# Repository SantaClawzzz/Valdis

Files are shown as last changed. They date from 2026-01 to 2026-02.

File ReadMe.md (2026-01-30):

# Valdis

## First test bench<br>
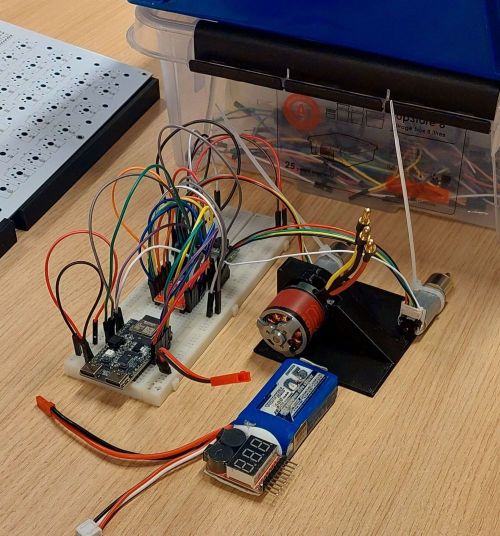
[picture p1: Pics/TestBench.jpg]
Test


## Info

**HETKEL PINOUT ON KÕIK VALE**<br>
Läksime üle PCB designile ja kasutuses nüüd ESP32 S3 (NanoS3)

**Mini-battle bot Läti võistluseks (450g)**

### Komponendid

* 3-phase relva mootor
* ESC ([Emax_bullet_35A](https://www.hobbydrone.cz/en/emax-bullet-35a/))
* 2x Mootorit liikumiseks (kursuse omad)
* 1x TB6612FNG ([Kiip](https://www.digikey.com/en/products/detail/toshiba-semiconductor-and-storage/tb6612fng-c-8-el/1730070) mitte breakout)
* 1x ESP32-S3 ([NanoS3](https://unexpectedmaker.com/shop.html#!/NanoS3/p/577095557/category=0))
* 3S aku
* USB-C ([USB4085-GF-A](https://www.digikey.com/en/products/detail/gct/USB4085-GF-A/9859662))
* Switching 3.3V ([RAA2118054GP3#JA0](https://www.digikey.com/en/products/detail/renesas-electronics-corporation/RAA2118054GP3-JA0/22162357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))

Kasutusse võtti ESP32-S3 (NanoS3 devkit)<br>
Meil vaja 13:<br>
* Driver võtab 3per mootor = 6 kokku
* Mootori enkooderid veel 2x2=4 kokku
* ESC võtab PWM, ehk 1 kokku
* EN nupp = 1 kokku
* Buzzer = 1 kokku

Lisaks on vaba pinne 7tk (+3 power pin):
* IO35
* IO36
* IO37
* IO9 (SCL)
* IO8 (SDA)
* RX
* TX

Power:
* 5V
* 3V3
* GND

### Keha

Keha tuleks Resin või mingi 3D print, kõik komponendid kaaluvad 202g, ehk 230g enam vähem mängimis ruumi.<br>
Enne tehtud proto (mis ka liiga väike), on 64g, et suht OK

Relvale teha mingi lindiga või sarnane ülekande mehhanism, et saaks mootori keresse peita ja ei saaks otse laksu teistelt

### Proge/RC

Kaugelt juhib läbi bluetoothi, arvatavasti sama millega Jaan juhib<br>
Puldiks võtta mingi Xbox controller millel on bluetooth receiver juba olemas

### MCU pinout

* Mootorid:
  * PWM
    * PWMA - IO15
    * PWMB - IO10
  * A IN
    * AIN2 - IO14
    * AIN1 - IO13
  * B IN
    * BIN2 - IO11
    * BIN1 - IO12

  * Enkooder Mootor 1 (A)
    * Kollane (B) - IO16
    * Roheline (A) - IO17
  * Enkooder Mootor 2 (B)
    * Kollane (B) - IO6
    * Rohleine (A) - IO7

* ESC PWM - IO18

* Buzzer - IO34

* DBG LED - IO5

* BAT VOL - IO1

### Power

* 12V aku - regulator - 3.3V
  * 3.3V toidab MCU ja DRV loogika ja enkooderi VCC
* 12V toidab DRV switching
* STBY - otse 3.3V ehk HIGH ja constant ON

Toite jaoks on analoog pin mis mõõdab seda
* Selle jaoks pinge jagur (1000R/200R, 12.6V/10.8V)
  * 2.1V when full
  * 1.8V when empty (just kui)

### Enkooder

Enkoodril on 7x35 impulssi pöörde kohta (just kui)<br>
Vaja teha koodis et kontrolliks kiirust ja hoiaks sama erinevalt pingest ja nh soidaks ka otse kui uks vasib ara

### ESC

ESC on väline, joodab otse külge, kannatab 35A ja on current surge protection ka olemas

### Switch

Power switch ühendub JST-PH-2.0 pistikuga, ja power lüliti kontroll on low-side FET

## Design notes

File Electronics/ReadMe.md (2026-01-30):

# Info

Skemaatik ja elektroonika muudatused kõik siia<br>

## Rev_1

Esimene rev mis ei jõudnud kaugemale arendusest oli joodetud otse protoboardile ESP-C6, TB6612FNG driver, buzzer, Regu ja headerid<br>
See ei läinud kasutusse sest on vaja S3 kergemaks Bluetooth ühenduseks, sest Liikmel juba kood olemas, C6 ei võimalda BluePad library (kui sain õigesti aru)

Seega S3 peale minek oli kõige loogilisem, aga S3 on palju suurem, uue ostmine pold halb idee, aga esimese deadline liikus edasi, sest unustasime regada, et läks korralikuma PCB designi peale, ehk Rev_2

## Rev_2

Teine Rev oli PCB design aga kasutades DevKiti, sest ei taha tekitada rohkem probleeme mida ei saa pärast hotfixiga parnada. Kui see töötab, siis ideaalis on Rev_3 see kui PCBl vahetatakse DevKit reaalse MCU-ga ära
Praegusel disainil on NanoS3, mis ei ole USB ühendusega, aga on toodud need pinnid välja. Switching regu on pandud selle toiteks ja LDO oleks võibolla old kahtlane (100-200mA ja 12.6V pealt 3.3V peale).

Loomulikult ka USB-C ja ka mitu erinevat headeri, mõned tavaliste gpiode jaoks, aku, switchi (power switch on FET controlled (Low side, sest high current suht)) ja ka mootorid.

Disain ise on 4 layer, Signal-GND-GND-Signal (Aku ja Fet polyd on kõigil neljal layeril, et oleks rohkem vaske jahutuseks)

Nano ise joodetakse SMD kujul peale, ning keskmine EPAD seal all samuti.

DBG LEDi kõrvale on veel kõigi 3 toite LEDid, 12V, 5V, 3V3

# Docs

## Schematic

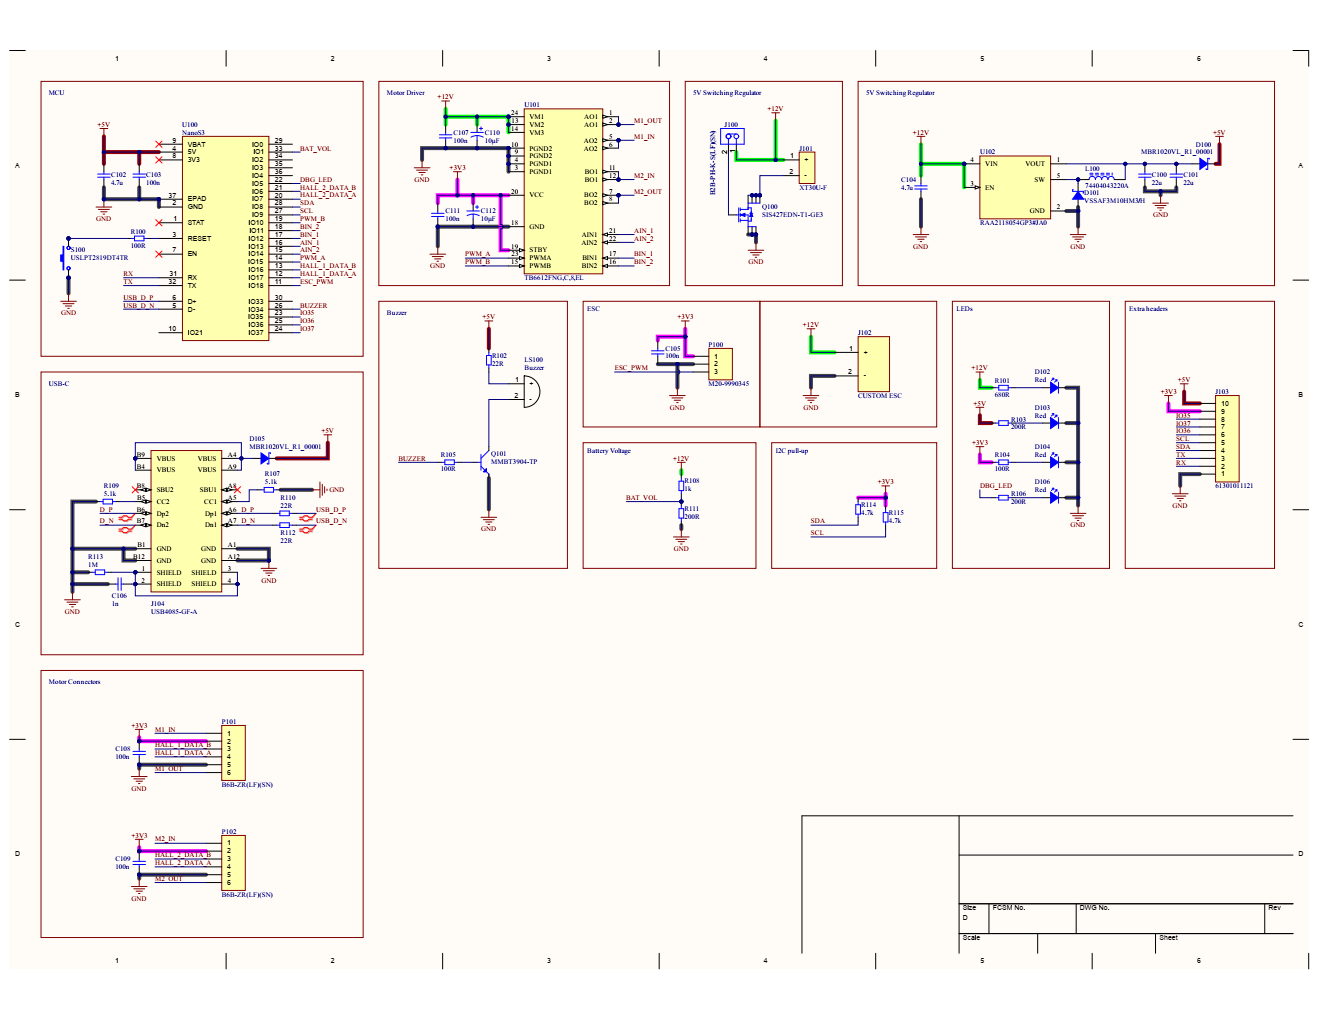
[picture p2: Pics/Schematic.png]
Schematic


## Layout

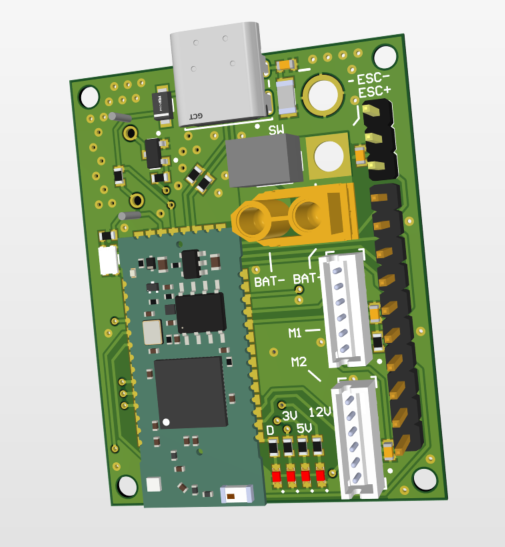
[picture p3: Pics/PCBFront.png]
PCBFront

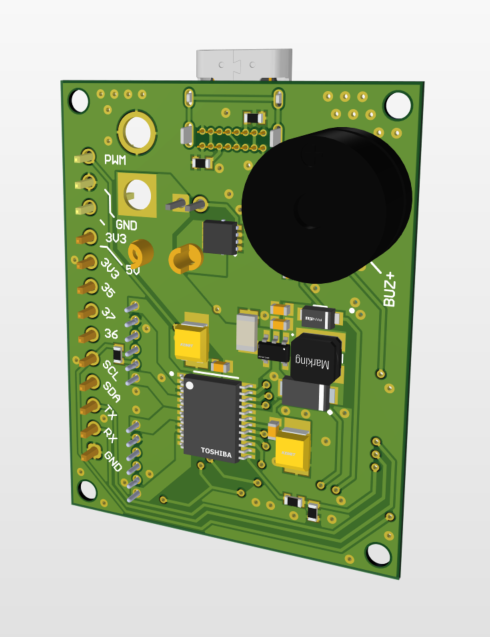
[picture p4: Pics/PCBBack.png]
PCBBack


## ESP32-S3 (NanoS3) pinout

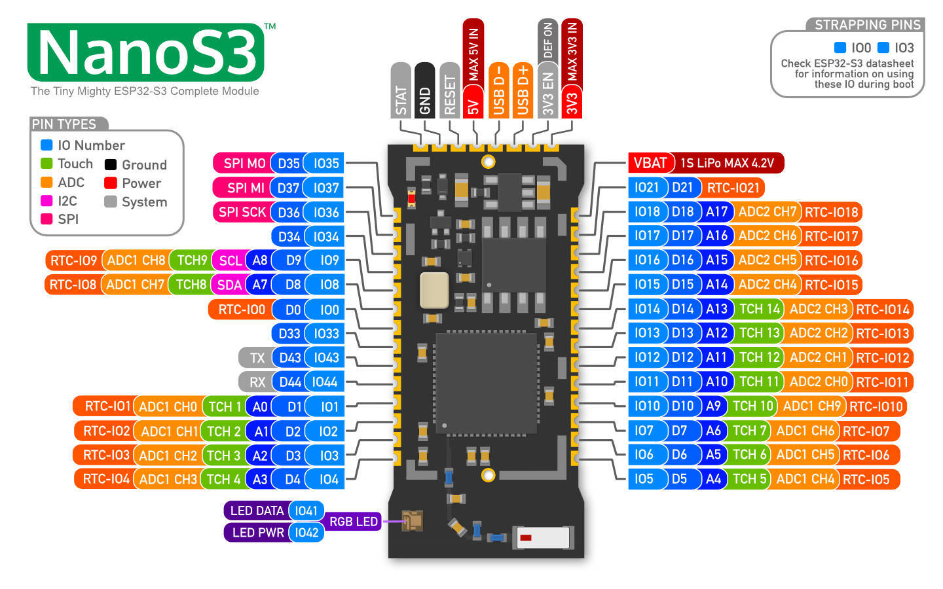
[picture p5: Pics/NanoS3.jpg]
ESPPinout


## Motor pinout

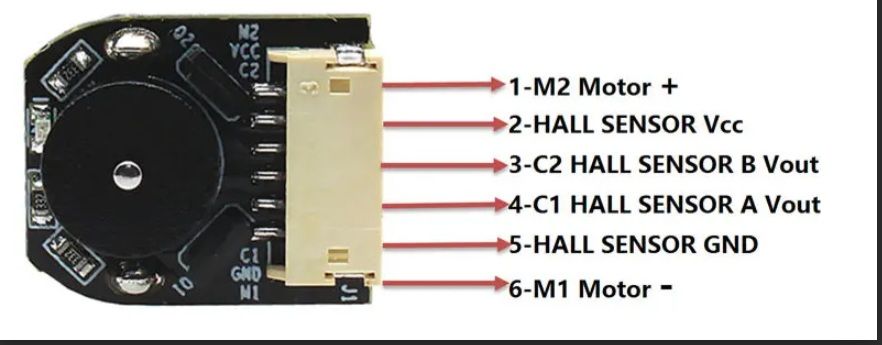
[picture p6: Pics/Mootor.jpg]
MotorPinout


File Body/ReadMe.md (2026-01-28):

# Info

Kui peaks mingi 3D mudelid või mingid pildid jms, siis tuleb siia
3D kehad PCBst on lisatud

# Docs

## Old Body 3D model

OldBody

## Body 3D model

Body

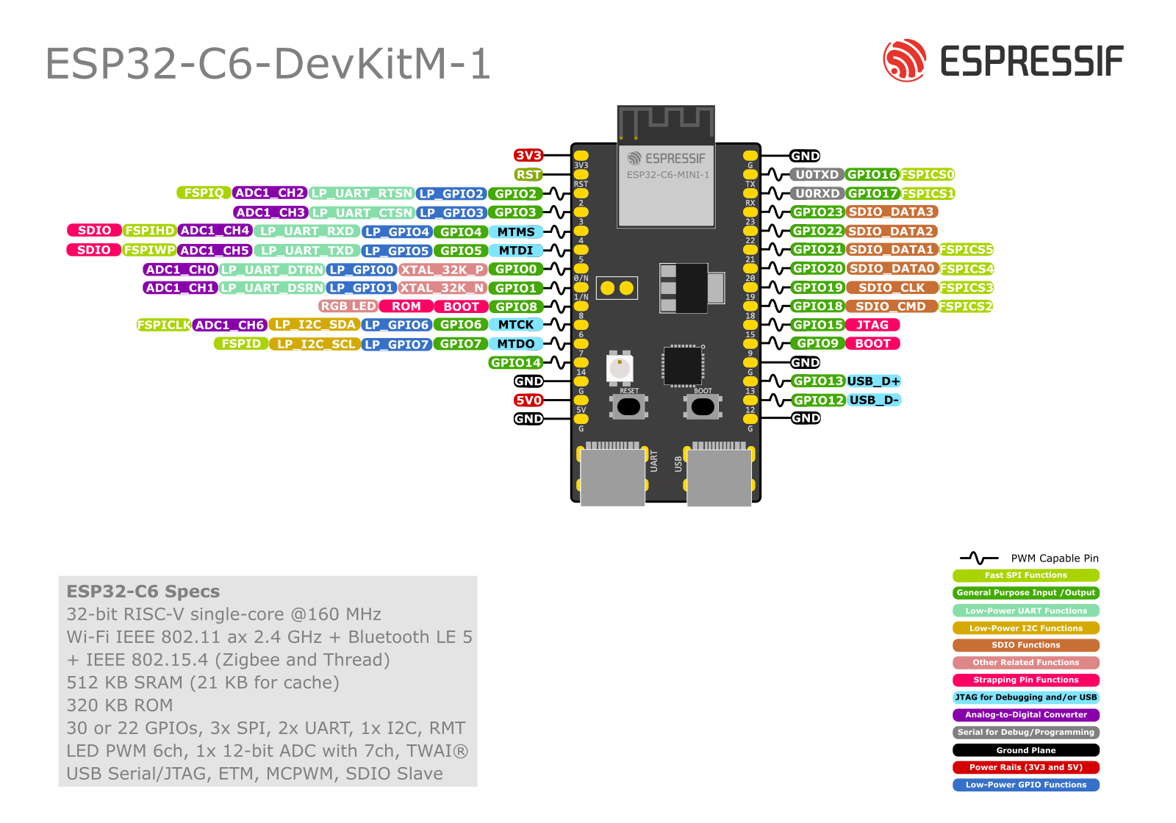
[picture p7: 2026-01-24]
Pics/ESP32-C6-DevKit-M1.png

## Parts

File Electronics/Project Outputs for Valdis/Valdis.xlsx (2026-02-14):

Comment | Description | Designator | Footprint | LibRef | Quantity
22u | MLCC, 0603, 22u, 10%, 16V, X5R | C100, C101 | MLCC_0603_M | CMP-001-1264-1 | 2
4.7u | MLCC, 0805, 4.7u, 10%, 50V, X5R | C102 | MLCC_0805_M | CMP-001-0828-2 | 1
100n | MLCC, 0603, 100n, 10%, 35V, X7R, MLCC, 0603, 100n, 10%, 50V, X7R | C103, C105, C107, C108, C109, C111 | MLCC_0603_M | CMP-001-0755-1, CMP-001-0815-1 | 6
4.7u | MLCC, 1206, 4.7u, 10%, 35V, X5R | C104 | MLCC_1206_M | CMP-001-1124-2 | 1
1n | MLCC, 0603, 1n, 10%, 50V, X7R | C106 | MLCC_0603_M | CMP-001-0786-1 | 1
T495B106K025ATE750 | 10UF Solid MNO2 Tantalum Electrolytic Capacitor, 25 V DC +/-10%, T495 Series | C110, C112 | 593D106X9025C2TE3-Footprint-1 | CMP-0001-00298-2 | 2
MBR1020VL_R1_00001 | Rectifier Diode, Schottky, 1 Phase, 1 Element, 1A, 20V V(RRM), Silicon | D100, D105 | FP-MBR1020VL_R1_00001-MFG | CMP-ROOT-01310-1 | 2
VSSAF3M10HM3/H | Rectifier Diode, Schottky, 1 Phase, 1 Element, 2.3A, 100V V(RRM), Silicon, DO-221AC | D101 | VSSAF3M10HM3_H-Footprint-1 | CMP-ROOT-01308-1 | 1
Red | Generic red 0603 LED | D102, D103, D104, D106 | 0603 RED LED | CMP-ROOT-00025-2 | 4
B2B-PH-K-S(LF)(SN) | Connector Header, PH Series, 2 Position, 2.00mm, Through Hole, Press-Fit, Solder, Natural | J100 | JST-B2B-PH-K-S_V | CMP-ROOT-01319-1 | 1
XT30U-F | Power Connector | J101 | XT30U-F | CMP-ROOT-01262-2 | 1
CUSTOM ESC | Custom ESC pinout | J102 | CUSTOM ESC-Footprint-1 | CMP-ROOT-01320-3 | 1
61301011121 | THT Vertical Pin Header WR-PHD, Pitch 2.54 mm, Single Row, 10 pins | J103 | 61301011121 | CMP-ROOT-01212-1 | 1
USB4085-GF-A | USB Connector, 16 Contact(s), Female, Right Angle, Solder Terminal, Locking, Receptacle | J104 | FP-USB4085-GF-A-MFG | CMP-001-1800-1 | 1
74404043220A | General Purpose Inductor, 22uH, 20%, 1 Element, Nickel-zinc Ferrite-Core, SMD, 1616 | L100 | WE-LQS_4025 | CMP-ROOT-01309-1 | 1
Buzzer | 7mm | LS100 | Buzzer-Footprint-1 | CMP-ROOT-01315-3 | 1
M20-9990345 | Connector Header Through Hole 3 position 0.100" (2.54mm) | P100 | 3Pos Pin Header | CMP-ROOT-00217-1 | 1
B6B-ZR(LF)(SN) | Header for PCB; pitch 1.50mm; 6-contacts; THT; male; top entry; 50V/1A | P101, P102 | FP-B6B-ZR-SM4-TF_LF_SN-MFG | CMP-ROOT-01270-3 | 2
SIS427EDN-T1-GE3 | Trans MOSFET P-CH 30V 15A 8-Pin PowerPAK EP T/R | Q100 | Copy of TPN2R304PL,L1Q-Footprint-1 | CMP-ROOT-01317-1 | 1
MMBT3904-TP | TRANS NPN 40V 0.2A SOT23 | Q101 | SOT-23-3 | CMP-ROOT-00274-1 | 1
100R | Resistor, 0603, 100R, 1%, 1/10W, Resistor, 0603, 100R, ≤5%, ≥1/16W | R100, R104, R105 | Resistor_0603_M | CMP-001-0054-5, CMP-0001-00262-1 | 3
680R | Resistor, 0603, 680R, 1%, 1/10W | R101 | Resistor_0603_M | CMP-001-0074-3 | 1
22R | Resistor, 0603, 22R, 1%, 1/10W | R102, R110, R112 | Resistor_0603_M | CMP-001-0038-3 | 3
200R | Resistor, 0603, 200R, 1%, 1/10W, Resistor, 0603, 220R, 1%, 1/10W | R103, R106, R111 | Resistor_0603_M | CMP-001-0060-2, CMP-001-0061-2 | 3
5.1k | Resistor, 0603, 5.1k, 1%, 1/10W | R107, R109 | Resistor_0603_M | CMP-001-0094-2 | 2
1k | Resistor, 0603, 1k, 0.1%, 1/16W | R108 | Resistor_0603_M | CMP-0001-00237-1 | 1
1M | Resistor, 1206, 1M, 1%, 1/4W | R113 | Resistor_1206_M | CMP-0001-00051-1 | 1
4.7k | Resistor, 0603, 4.7k, 1%, 1/10W | R114, R115 | Resistor_0603_M | CMP-001-0093-2 | 2
USLPT2819DT4TR | Keypad Switch, SPST, 0.05A, 1.96N, Solder Terminal, Panel Mount | S100 | USLPT2819DT4TR-Footprint-1 | CMP-ROOT-01290-3 | 1
NanoS3 | Unexpected Maker's NanoS3 DevKit | U100 | NanoS3 | CMP-00023-1 | 1
TB6612FNG,C,8,EL | DC Motor Driver 2.7V to 5.5V 24-Pin SSOP Embossed T/R | U101 | FP-SSOP24-P-300-0_65A-MFG | CMP-00025-1 | 1
RAA2118054GP3#JA0 | Switching Regulator, Current-mode, 0.3A, 230kHz Switching Freq-Max, PDSO5 | U102 | P5_064B_MFG | CMP-00019-3 | 1

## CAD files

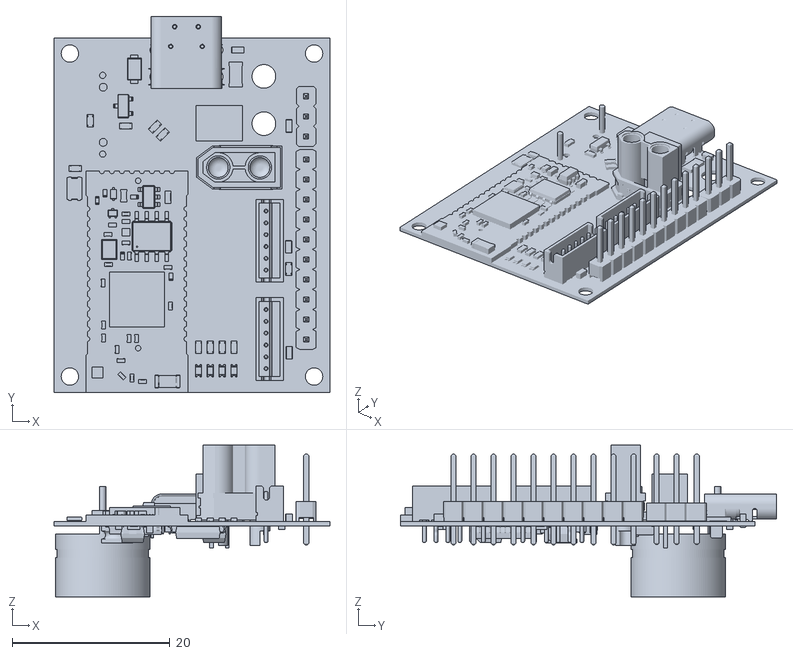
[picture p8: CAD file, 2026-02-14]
Body/Valdis.stl
35.0 x 47.7 x 19.3

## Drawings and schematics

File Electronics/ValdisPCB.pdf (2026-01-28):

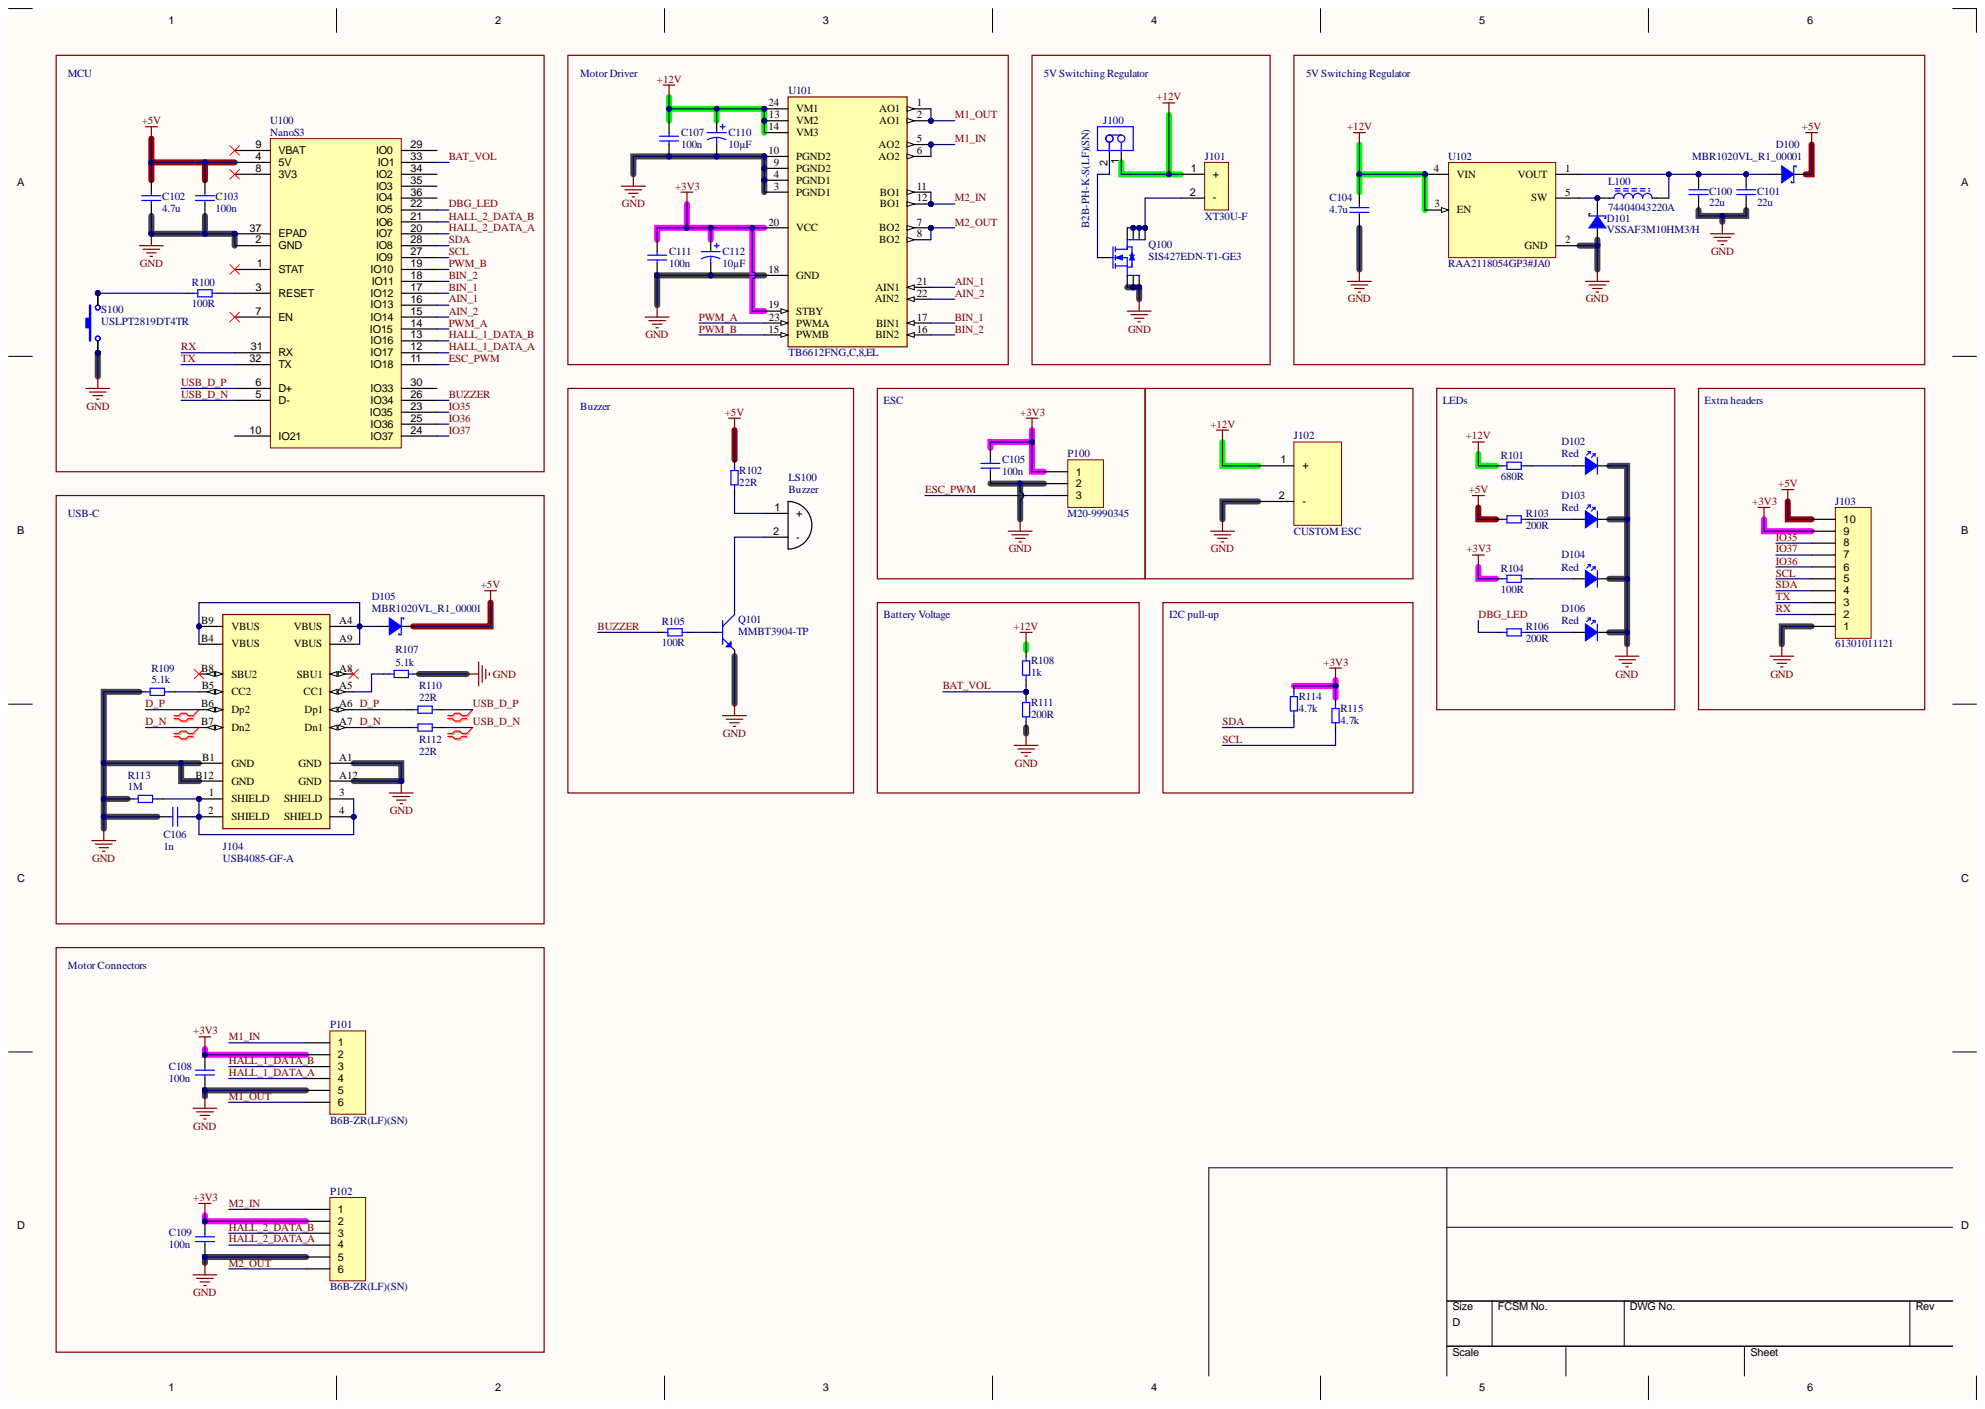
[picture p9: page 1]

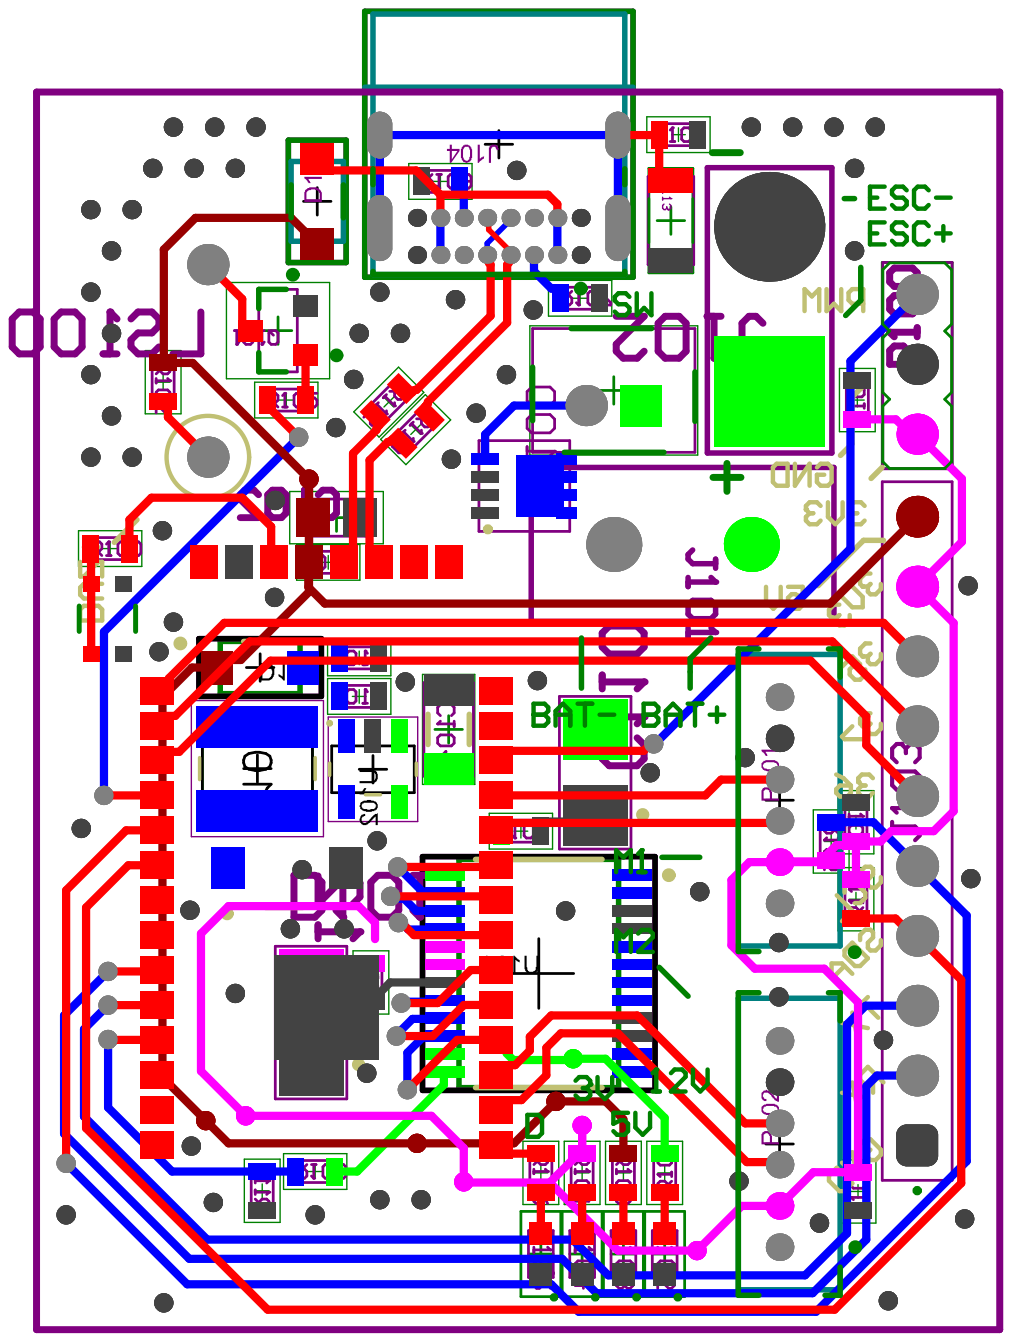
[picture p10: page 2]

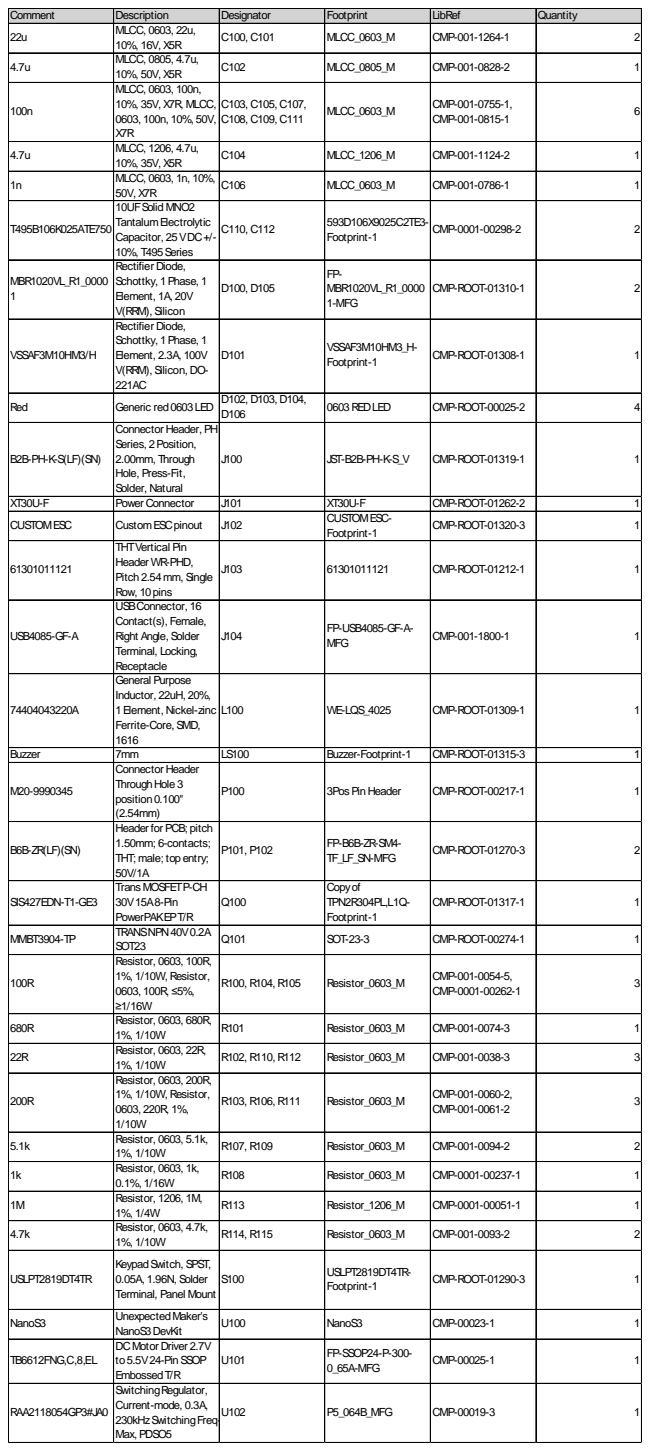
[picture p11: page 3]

Comment | Description | Designator | Footprint | LibRef | Quantity
22u | MLCC, 0603, 22u, 10%, 16V, X5R | C100, C101 | MLCC_0603_M | CMP-001-1264-1 | 2

4.7u | MLCC, 0805, 4.7u, 10%, 50V, X5R | C102 | MLCC_0805_M | CMP-001-0828-2 | 1

100n | MLCC, 0603, 100n, 10%, 35V, X7R, MLCC, 0603, 100n, 10%, 50V, X7R | C103, C105, C107, C108, C109, C111 | MLCC_0603_M | CMP-001-0755-1, CMP-001-0815-1 | 6

4.7u | MLCC, 1206, 4.7u, 10%, 35V, X5R | C104 | MLCC_1206_M | CMP-001-1124-2 | 1

1n | MLCC, 0603, 1n, 10%, 50V, X7R | C106 | MLCC_0603_M | CMP-001-0786-1 | 1

T495B106K025ATE750 | 10UFSolid MNO2 TantalumElectrolytic Capacitor, 25VDC+/-10%, T495Series | C110, C112 | 593D106X9025C2TE3-Footprint-1 | CMP-0001-00298-2 | 2

MBR1020VL_R1_0000 1 | Rectifier Diode, Schottky, 1Phase, 1 Element, 1A, 20V V(RRM), Silicon | D100, D105 | FP-MBR1020VL_R1_0000 1-MFG | CMP-ROOT-01310-1 | 2

VSSAF3M10HM3/H | Rectifier Diode, Schottky, 1Phase, 1 Element, 2.3A, 100V V(RRM), Silicon, DO-221AC | D101 | VSSAF3M10HM3_H-Footprint-1 | CMP-ROOT-01308-1 | 1

Red | Generic red0603LED | D102, D103, D104, D106 | 0603REDLED | CMP-ROOT-00025-2 | 4

B2B-PH-K-S(LF)(SN) | Connector Header, PH Series, 2Position, 2.00mm, Through Hole, Press-Fit, Solder, Natural | J100 | JST-B2B-PH-K-S_V | CMP-ROOT-01319-1 | 1

XT30U-F | Power Connector | J101 | XT30U-F | CMP-ROOT-01262-2 | 1
CUSTOMESC | CustomESCpinout | J102 | CUSTOMESC-Footprint-1 | CMP-ROOT-01320-3 | 1

61301011121 | THTVertical Pin Header WR-PHD, Pitch 2.54mm, Single Row, 10pins | J103 | 61301011121 | CMP-ROOT-01212-1 | 1

USB4085-GF-A | USBConnector, 16 Contact(s), Female, Right Angle, Solder Terminal, Locking, Receptacle | J104 | FP-USB4085-GF-A-MFG | CMP-001-1800-1 | 1

74404043220A | General Purpose Inductor, 22uH, 20%, 1Element, Nickel-zinc Ferrite-Core, SMD, 1616 | L100 | WE-LQS_4025 | CMP-ROOT-01309-1 | 1

Buzzer | 7mm | LS100 | Buzzer-Footprint-1 | CMP-ROOT-01315-3 | 1
M20-9990345 | Connector Header ThroughHole 3 position0.100" (2.54mm) | P100 | 3PosPin Header | CMP-ROOT-00217-1 | 1

B6B-ZR(LF)(SN) | Header for PCB; pitch 1.50mm; 6-contacts; THT; male; topentry; 50V/1A | P101, P102 | FP-B6B-ZR-SM4-TF_LF_SN-MFG | CMP-ROOT-01270-3 | 2

SIS427EDN-T1-GE3 | TransMOSFETP-CH 30V15A8-Pin PowerPAKEPT/R | Q100 | Copyof TPN2R304PL,L1Q-Footprint-1 | CMP-ROOT-01317-1 | 1

MMBT3904-TP | TRANSNPN40V0.2A SOT23 | Q101 | SOT-23-3 | CMP-ROOT-00274-1 | 1

100R | Resistor, 0603, 100R, 1%, 1/10W, Resistor, 0603, 100R, ≤5%, ≥1/16W | R100, R104, R105 | Resistor_0603_M | CMP-001-0054-5, CMP-0001-00262-1 | 3

680R | Resistor, 0603, 680R, 1%, 1/10W | R101 | Resistor_0603_M | CMP-001-0074-3 | 1

22R | Resistor, 0603, 22R, 1%, 1/10W | R102, R110, R112 | Resistor_0603_M | CMP-001-0038-3 | 3

200R | Resistor, 0603, 200R, 1%, 1/10W, Resistor, 0603, 220R, 1%, 1/10W | R103, R106, R111 | Resistor_0603_M | CMP-001-0060-2, CMP-001-0061-2 | 3

5.1k | Resistor, 0603, 5.1k, 1%, 1/10W | R107, R109 | Resistor_0603_M | CMP-001-0094-2 | 2

1k | Resistor, 0603, 1k, 0.1%, 1/16W | R108 | Resistor_0603_M | CMP-0001-00237-1 | 1

1M | Resistor, 1206, 1M, 1%, 1/4W | R113 | Resistor_1206_M | CMP-0001-00051-1 | 1

4.7k | Resistor, 0603, 4.7k, 1%, 1/10W | R114, R115 | Resistor_0603_M | CMP-001-0093-2 | 2

USLPT2819DT4TR | KeypadSwitch, SPST, 0.05A, 1.96N, Solder Terminal, Panel Mount | S100 | USLPT2819DT4TR-Footprint-1 | CMP-ROOT-01290-3 | 1

NanoS3 | UnexpectedMaker's NanoS3DevKit | U100 | NanoS3 | CMP-00023-1 | 1

TB6612FNG,C,8,EL | DCMotor Driver 2.7V to5.5V24-PinSSOP EmbossedT/R | U101 | FP-SSOP24-P-300-0_65A-MFG | CMP-00025-1 | 1

RAA2118054GP3#JA0 | SwitchingRegulator, Current-mode, 0.3A, 230kHzSwitchingFreq-Max, PDSO5 | U102 | P5_064B_MFG | CMP-00019-3 | 1

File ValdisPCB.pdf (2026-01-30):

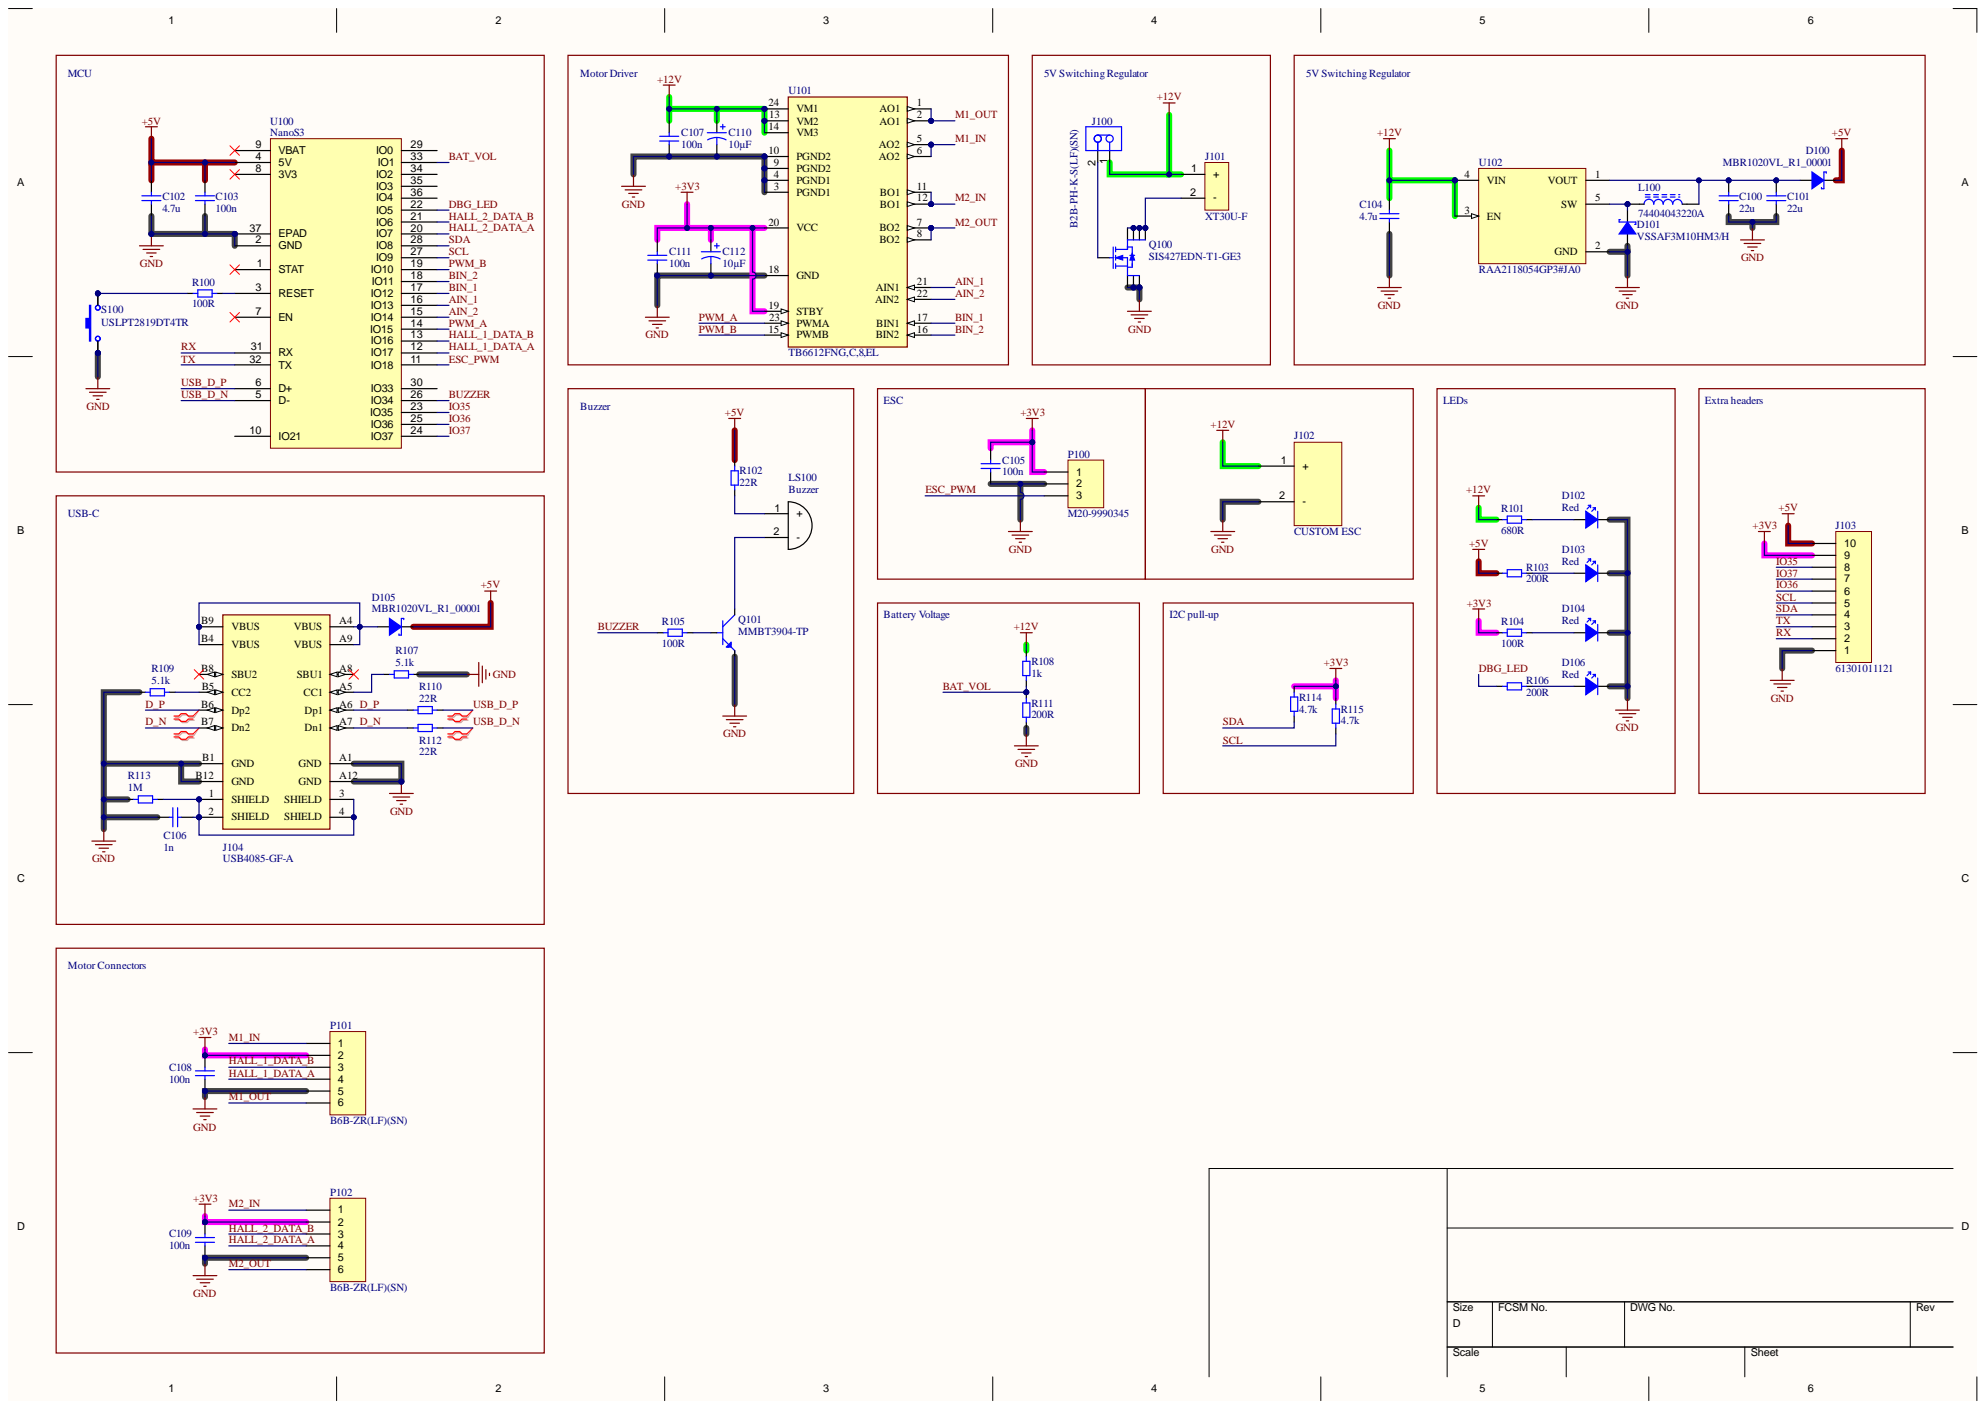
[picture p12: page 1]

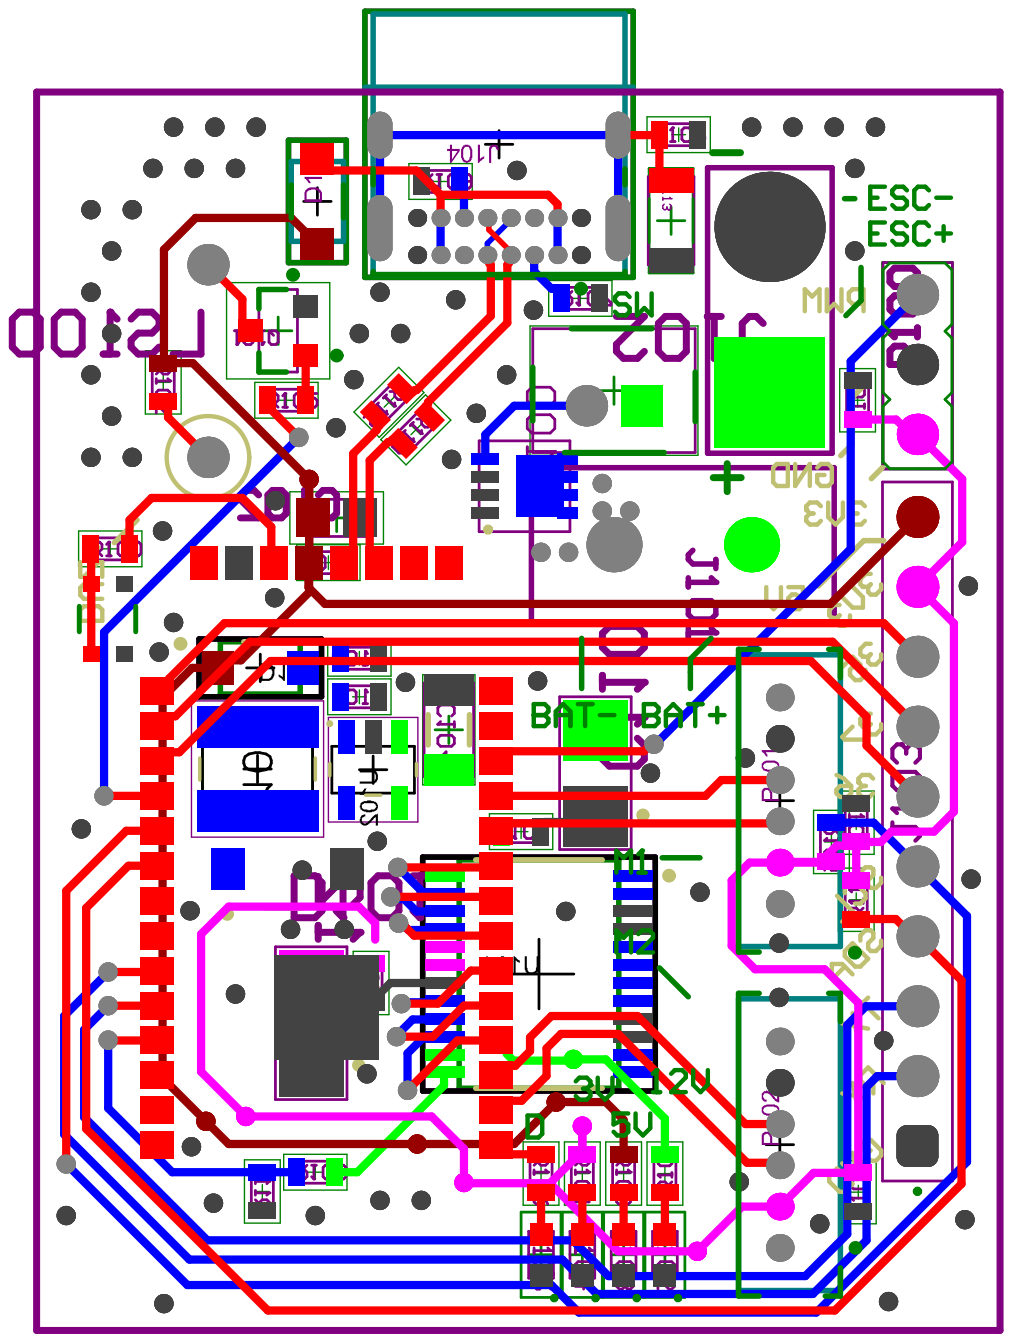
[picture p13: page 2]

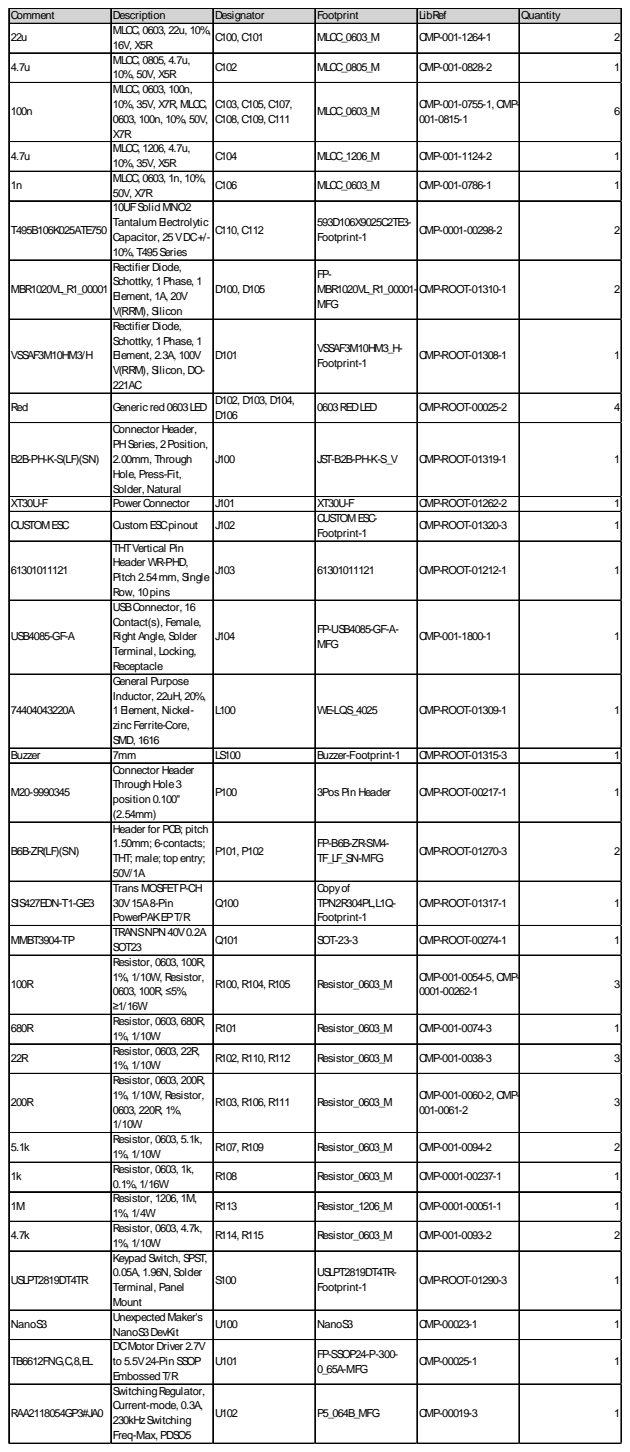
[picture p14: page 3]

Comment | Description | Designator | Footprint | LibRef | Quantity
22u | MLCC, 0603, 22u, 10%, 16V, X5R | C100, C101 | MLCC_0603_M | CMP-001-1264-1 | 2

4.7u | MLCC, 0805, 4.7u, 10%, 50V, X5R | C102 | MLCC_0805_M | CMP-001-0828-2 | 1

100n | MLCC, 0603, 100n, 10%, 35V, X7R, MLCC, 0603, 100n, 10%, 50V, X7R | C103, C105, C107, C108, C109, C111 | MLCC_0603_M | CMP-001-0755-1, CMP-001-0815-1 | 6

4.7u | MLCC, 1206, 4.7u, 10%, 35V, X5R | C104 | MLCC_1206_M | CMP-001-1124-2 | 1

1n | MLCC, 0603, 1n, 10%, 50V, X7R | C106 | MLCC_0603_M | CMP-001-0786-1 | 1

T495B106K025ATE750 | 10UFSolid MNO2 Tantalum Electrolytic Capacitor, 25VDC+/-10%, T495Series | C110, C112 | 593D106X9025C2TE3-Footprint-1 | CMP-0001-00298-2 | 2

MBR1020VL_R1_00001 | Rectifier Diode, Schottky, 1Phase, 1 Element, 1A, 20V V(RRM), Silicon | D100, D105 | FP-MBR1020VL_R1_00001-MFG | CMP-ROOT-01310-1 | 2

VSSAF3M10HM3/H | Rectifier Diode, Schottky, 1Phase, 1 Element, 2.3A, 100V V(RRM), Silicon, DO-221AC | D101 | VSSAF3M10HM3_H-Footprint-1 | CMP-ROOT-01308-1 | 1

Red | Generic red 0603LED | D102, D103, D104, D106 | 0603REDLED | CMP-ROOT-00025-2 | 4

B2B-PH-K-S(LF)(SN) | Connector Header, PHSeries, 2Position, 2.00mm, Through Hole, Press-Fit, Solder, Natural | J100 | JST-B2B-PH-K-S_V | CMP-ROOT-01319-1 | 1

XT30U-F | Power Connector | J101 | XT30U-F | CMP-ROOT-01262-2 | 1
CUSTOMESC | Custom ESCpinout | J102 | CUSTOMESC-Footprint-1 | CMP-ROOT-01320-3 | 1

61301011121 | THTVertical Pin Header WR-PHD, Pitch 2.54mm, Single Row, 10pins | J103 | 61301011121 | CMP-ROOT-01212-1 | 1

USB4085-GF-A | USBConnector, 16 Contact(s), Female, Right Angle, Solder Terminal, Locking, Receptacle | J104 | FP-USB4085-GF-A-MFG | CMP-001-1800-1 | 1

74404043220A | General Purpose Inductor, 22uH, 20%, 1Element, Nickel-zinc Ferrite-Core, SMD, 1616 | L100 | WE-LQS_4025 | CMP-ROOT-01309-1 | 1

Buzzer | 7mm | LS100 | Buzzer-Footprint-1 | CMP-ROOT-01315-3 | 1
M20-9990345 | Connector Header Through Hole3 position 0.100" (2.54mm) | P100 | 3PosPin Header | CMP-ROOT-00217-1 | 1

B6B-ZR(LF)(SN) | Header for PCB; pitch 1.50mm; 6-contacts; THT; male; top entry; 50V/1A | P101, P102 | FP-B6B-ZR-SM4-TF_LF_SN-MFG | CMP-ROOT-01270-3 | 2

SIS427EDN-T1-GE3 | Trans MOSFETP-CH 30V15A8-Pin PowerPAKEPT/R | Q100 | Copyof TPN2R304PL,L1Q-Footprint-1 | CMP-ROOT-01317-1 | 1

MMBT3904-TP | TRANSNPN 40V0.2A SOT23 | Q101 | SOT-23-3 | CMP-ROOT-00274-1 | 1

100R | Resistor, 0603, 100R, 1%, 1/10W, Resistor, 0603, 100R, ≤5%, ≥1/16W | R100, R104, R105 | Resistor_0603_M | CMP-001-0054-5, CMP-0001-00262-1 | 3

680R | Resistor, 0603, 680R, 1%, 1/10W | R101 | Resistor_0603_M | CMP-001-0074-3 | 1

22R | Resistor, 0603, 22R, 1%, 1/10W | R102, R110, R112 | Resistor_0603_M | CMP-001-0038-3 | 3

200R | Resistor, 0603, 200R, 1%, 1/10W, Resistor, 0603, 220R, 1%, 1/10W | R103, R106, R111 | Resistor_0603_M | CMP-001-0060-2, CMP-001-0061-2 | 3

5.1k | Resistor, 0603, 5.1k, 1%, 1/10W | R107, R109 | Resistor_0603_M | CMP-001-0094-2 | 2

1k | Resistor, 0603, 1k, 0.1%, 1/16W | R108 | Resistor_0603_M | CMP-0001-00237-1 | 1

1M | Resistor, 1206, 1M, 1%, 1/4W | R113 | Resistor_1206_M | CMP-0001-00051-1 | 1

4.7k | Resistor, 0603, 4.7k, 1%, 1/10W | R114, R115 | Resistor_0603_M | CMP-001-0093-2 | 2

USLPT2819DT4TR | Keypad Switch, SPST, 0.05A, 1.96N, Solder Terminal, Panel Mount | S100 | USLPT2819DT4TR-Footprint-1 | CMP-ROOT-01290-3 | 1

NanoS3 | Unexpected Maker's NanoS3DevKit | U100 | NanoS3 | CMP-00023-1 | 1

TB6612FNG,C,8,EL | DCMotor Driver 2.7V to 5.5V24-Pin SSOP Embossed T/R | U101 | FP-SSOP24-P-300-0_65A-MFG | CMP-00025-1 | 1

RAA2118054GP3#JA0 | SwitchingRegulator, Current-mode, 0.3A, 230kHzSwitching Freq-Max, PDSO5 | U102 | P5_064B_MFG | CMP-00019-3 | 1

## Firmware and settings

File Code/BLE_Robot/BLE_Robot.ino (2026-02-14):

/*
 * BLE HID Gamepad Client Example
 *
 * This example demonstrates how to connect to a BLE HID Gamepad and read its input.
 * The ESP32 acts as a BLE Central (client) that connects to a BLE gamepad peripheral.
 *
 * Features:
 * - Scans for BLE HID gamepad devices
 * - Connects to the first gamepad found
 * - Secure pairing with bonding
 * - Subscribes to input report notifications
 * - Parses and displays gamepad input (buttons and axes)
 * - Automatic reconnection on disconnect
 *
 * Usage:
 * 1. Upload this sketch to your ESP32
 * 2. Turn on your BLE gamepad (or run the Server_Gamepad example on another ESP32)
 * 3. The ESP32 will scan, connect, and display gamepad input in the serial monitor
 *
 * Note: This example uses "Just Works" pairing for automatic connection without
 * PIN entry or confirmation. The bond is saved for future connections.
 *
 * Compatible with gamepads using the standard HID Report Descriptor format
 *
 * Created by lucasssvaz
 */

#include <BLEDevice.h>
#include <BLESecurity.h>
#include <ESP32Servo.h>

// Defines
#define DBG 5
#define PWM_A 15
#define PWM_B 10
#define ESC 18
#define AIN1 13
#define AIN2 14
#define BIN1 12
#define BIN2 11
#define BUZ 34

Servo esc;

int state = 0;

// HID Service UUID (standard UUID for HID over GATT)
static BLEUUID hidServiceUUID((uint16_t)0x1812);
// HID Report characteristic UUID (used for input/output reports)
static BLEUUID reportCharUUID((uint16_t)0x2A4D);
// HID Report Map characteristic UUID
static BLEUUID reportMapUUID((uint16_t)0x2A4B);

static boolean doConnect = false;
static boolean connected = false;
static boolean doScan = false;
static BLERemoteCharacteristic *pInputReportCharacteristic = nullptr;
static BLEAdvertisedDevice *myDevice = nullptr;
static BLEClient *pClient = nullptr;

// Gamepad report structure (adjust based on your gamepad's report descriptor)
// This matches the Server_Gamepad example format
struct GamepadReport {
  uint8_t reportId;  // Report ID
  int8_t x;          // X axis (-127 to 127)
  int8_t y;          // Y axis (-127 to 127)
  uint8_t buttons;   // 8 buttons (bit 0-7)
} __attribute__((packed));

// Callback function to handle gamepad input notifications
static void notifyCallback(BLERemoteCharacteristic *pBLERemoteCharacteristic, uint8_t *pData, size_t length, bool isNotify) {
  Serial.printf("Received %d bytes: ", length);

  // Check if data length matches our expected gamepad report
  if (length == sizeof(GamepadReport)) {
    GamepadReport *report = (GamepadReport *)pData;

    //BUZZER
    bool pressed = report -> buttons & 0x01;
    analogWrite(BUZ, pressed ? 200 : 0);

    //ESC
    /* ESC button control
    bool ESC_BUT = report -> buttons & 0x02;
    if (ESC_BUT == 1){
      servo.write(100);
    }
    */

    /*Analog ESC control
    int minPulse = map(1000, 0, 20000, 0, 4095); // 1ms  
    int maxPulse = map(2000, 0, 20000, 0, 4095); // 2ms  
    int pulse = 0;
    if (state < 50) {
      analogWrite(ESC, minPulse); // low
      state ++;
    } else if (state < 100){
      analogWrite(ESC, 0);
      state ++;
    } else {
      analogWrite(ESC, maxPulse);
    }
    */

    //ESC with servo control
    int pulse = 1;
    if (state < 10){
      esc.writeMicroseconds(1000);
      state++;
    } else if (state < 50) {
      esc.writeMicroseconds(0);
      state++;
    } else if (state <= 100) {
      esc.writeMicroseconds(pulse*40);
      pulse++, state++;
    } else if (state < 120) {
      Serial.print("FULL THROTTLE ESC");
    }

    //MOTORS
    int8_t y = report ->y;
    int8_t base = abs(y);
    int8_t x = report ->x;
    int8_t yA = base;
    int8_t yB = base;
    
    if (x>30){
      yA = max(0, base - abs(x)); //Edit multiplier (0.8) to decrease sensitivity
    } else if (x<-30) {
      yB = max(0, base - abs(x));
    }

    // Determine motor direction
    bool forward = y > 30;
    bool backward = y < -30;

    /*
    // Set motor directions
    digitalWrite(AIN1, forward ? HIGH : backward ? LOW : LOW);
    digitalWrite(AIN2, forward ? LOW : backward ? HIGH : LOW);
    digitalWrite(BIN1, forward ? HIGH : backward ? LOW : LOW);
    digitalWrite(BIN2, forward ? LOW : backward ? HIGH : LOW);
    */

    if (forward) {
      digitalWrite(BIN1, HIGH);
      digitalWrite(BIN2, LOW);
    }
    else if (backward) {
      digitalWrite(BIN1, LOW);
      digitalWrite(BIN2, HIGH);
    }
    else {
      digitalWrite(BIN1, HIGH);
      digitalWrite(BIN2, LOW);
    }

    // Set motor speeds
    int16_t pwmA = 0;
    int16_t pwmB = 0;

    if (forward || backward) {
      pwmA = yA * 2;
      pwmB = yB * 2;
    }

    //Serial.printf("Wrote: %d on A and %d on B", pwmA, pwmB);
    analogWrite(PWM_A, pwmA);
    analogWrite(PWM_B, pwmB);

    Serial.printf("ID=%d, X=%4d, Y=%4d, Buttons=0x%02X [", report->reportId, report->x, report->y, report->buttons);

    // Display which buttons are pressed
    for (int i = 0; i < 8; i++) {
      if (report->buttons & (1 << i)) {
        Serial.printf("%d ", i + 1);
      }
    }
    Serial.println("]");
  } else {
    // Unknown format, just display hex dump
    Serial.print("Raw data: ");
    for (size_t i = 0; i < length; i++) {
      Serial.printf("%02X ", pData[i]);
    }
    Serial.println();
  }
}

// Client callbacks to handle connection events
class MyClientCallback : public BLEClientCallbacks {
  void onConnect(BLEClient *pclient) {
    Serial.println("Connected to gamepad");
  }

  void onDisconnect(BLEClient *pclient) {
    connected = false;
    Serial.println("Disconnected from gamepad");
  }
};

// Function to connect to the gamepad
bool connectToServer() {
  Serial.print("Connecting to gamepad at ");
  Serial.println(myDevice->getAddress().toString().c_str());

  pClient = BLEDevice::createClient();
  Serial.println(" - Created client");

  pClient->setClientCallbacks(new MyClientCallback());

  // Connect to the gamepad
  pClient->connect(myDevice);
  Serial.println(" - Connected to server");
  pClient->setMTU(185);  // Set MTU for larger data transfers

  // Obtain a reference to the HID service
  BLERemoteService *pRemoteService = pClient->getService(hidServiceUUID);
  if (pRemoteService == nullptr) {
    Serial.println("Failed to find HID service");
    pClient->disconnect();
    return false;
  }
  Serial.println(" - Found HID service");

  // Get all characteristics to find input reports
  std::map<std::string, BLERemoteCharacteristic *> *pCharMap = pRemoteService->getCharacteristics();

  // Look for input report characteristics (UUID 0x2A4D)
  for (auto const &entry : *pCharMap) {
    BLERemoteCharacteristic *pChar = entry.second;

    if (pChar->getUUID().equals(reportCharUUID)) {
      // Check if this characteristic has notify property (input report)
      if (pChar->canNotify()) {
        Serial.printf(" - Found input report characteristic (handle: 0x%04X)\n", pChar->getHandle());

        // Try to read Report Reference Descriptor to identify report type and ID
        BLERemoteDescriptor *pReportRefDesc = pChar->getDescriptor(BLEUUID((uint16_t)0x2908));
        if (pReportRefDesc != nullptr) {
          String refValue = pReportRefDesc->readValue();
          if (refValue.length() >= 2) {
            uint8_t reportId = refValue[0];
            uint8_t reportType = refValue[1];
            Serial.printf("   Report ID: %d, Type: %d (1=Input, 2=Output, 3=Feature)\n", reportId, reportType);

            // We want input reports (type = 1)
            if (reportType == 1) {
              pInputReportCharacteristic = pChar;
            }
          }
        } else {
          // No report reference descriptor, assume it's an input report
          pInputReportCharacteristic = pChar;
        }
      }
    }
  }

  if (pInputReportCharacteristic == nullptr) {
    Serial.println("Failed to find input report characteristic");
    pClient->disconnect();
    return false;
  }

  // Subscribe to input report notifications
  Serial.println(" - Subscribing to input report notifications");
  pInputReportCharacteristic->registerForNotify(notifyCallback);

  connected = true;
  Serial.println("Successfully connected and subscribed to gamepad!");

  // Note: Security/encryption will be automatically handled by the BLE stack
  // when the HID device requires it (using "Just Works" pairing).

  return true;
}

// Scan callback to detect gamepad devices
class MyAdvertisedDeviceCallbacks : public BLEAdvertisedDeviceCallbacks {
  void onResult(BLEAdvertisedDevice advertisedDevice) {
    Serial.print("BLE Device found: ");
    Serial.print(advertisedDevice.toString().c_str());

    // Check if device advertises HID service
    if (advertisedDevice.haveServiceUUID() && advertisedDevice.isAdvertisingService(hidServiceUUID)) {
      Serial.print(" - HID Device!");

      // Check if it's a gamepad by appearance (0x03C4 = HID Gamepad)
      if (advertisedDevice.haveAppearance()) {
        uint16_t appearance = advertisedDevice.getAppearance();
        Serial.printf(" (Appearance: 0x%04X)", appearance);
        if (appearance == 0x03C4) {
          Serial.print(" - GAMEPAD!");
        }
      }
      Serial.println();

      // Stop scanning and connect
      BLEDevice::getScan()->stop();
      myDevice = new BLEAdvertisedDevice(advertisedDevice);
      doConnect = true;
      doScan = true;
    } else {
      Serial.println();
    }
  }
};

void setup() {
  Serial.begin(115200);
  Serial.println("\n=== BLE HID Gamepad Client ===");
  Serial.println("Scanning for BLE HID gamepads...\n");

  // ESC servo control
  esc.attach(ESC, 1000, 2000);

  /* Analog ESC control code
  analogWriteFrequency(ESC, 50);
  analogWriteResolution(12,12);
  */

  BLEDevice::init("ESP32-Gamepad-Client");

  // Configure BLE Security for pairing with HID devices
  BLESecurity *pSecurity = new BLESecurity();

  // Set security capabilities and authentication mode
  // HID devices typically use "Just Works" pairing (no MITM) with bonding

  // Set IO capability to NONE for "Just Works" pairing
  pSecurity->setCapability(ESP_IO_CAP_NONE);

  // Bonding, no MITM, secure connections (for "Just Works" pairing)
  pSecurity->setAuthenticationMode(true, false, true);

  // Set security callbacks (using default implementation)
  BLEDevice::setSecurityCallbacks(new BLESecurityCallbacks());

  Serial.println("Security configured: Bonding + Secure Connections\n");

  // Create scanner and set callbacks
  BLEScan *pBLEScan = BLEDevice::getScan();
  pBLEScan->setAdvertisedDeviceCallbacks(new MyAdvertisedDeviceCallbacks());
  pBLEScan->setInterval(1349);
  pBLEScan->setWindow(449);
  pBLEScan->setActiveScan(true);
  pBLEScan->start(5, false);

  //User Code
  pinMode(PWM_A, OUTPUT);
  pinMode(PWM_B, OUTPUT);
  pinMode(ESC, OUTPUT);

  //Motor IN pins
  pinMode(AIN1, OUTPUT);
  pinMode(AIN2, OUTPUT);
  pinMode(BIN1, OUTPUT);
  pinMode(BIN2, OUTPUT);

  //LED
  pinMode(DBG, OUTPUT);

  //Buzzer
  pinMode(BUZ, OUTPUT);
}

void loop() {
  // Connect to gamepad if found
  if (doConnect == true) {
    if (connectToServer()) {
      Serial.println("\n*** Ready to receive gamepad input ***\n");
    } else {
      Serial.println("Failed to connect to gamepad");
    }
    doConnect = false;
  }

  // Restart scanning if disconnected
  if (!connected && doScan) {
    Serial.println("\nScanning for gamepads...");
    BLEDevice::getScan()->start(5, false);
    delay(1000);
  }

  delay(100);
}

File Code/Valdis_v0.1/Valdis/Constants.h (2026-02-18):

#ifndef CONSTANTS_H
#define CONSTANTS_H

// Serial logging switch for all debug prints.
// true  -> enable Serial prints
// false -> disable Serial prints
#define SERIAL_PRINT_ENABLED true

// Select one of two robots. Selection only changes allowed controller MAC.
#define VALDIS 1
#define KAUPO 2

//VALI AKTIIVNE ROBOT
#define ACTIVE_ROBOT KAUPO

#if ACTIVE_ROBOT == VALDIS
  #define CONTROLLER_MAC "40:8e:2c:76:9c:f4"
#elif ACTIVE_ROBOT == KAUPO
  #define CONTROLLER_MAC "ac:8e:bd:5c:9d:ce"
#else
  #error "ACTIVE_ROBOT must be VALDIS or KAUPO"
#endif

// Weapon speeds configured from controller buttons.
// X button sets WEAPON_SPEED_X, Y button sets WEAPON_SPEED_Y.
#define WEAPON_SPEED_X 255
#define WEAPON_SPEED_Y 128

// Joystick deadzone used for motor throttle mapping.
#define JOYSTICK_DEADZONE 15

// pin assignments - not including encoders
#define PWMA 15
#define PWMB 10
#define ESC 18
#define AIN1 13
#define AIN2 14
#define BIN1 12
#define BIN2 11
#define MBEA 7
#define MBEB 6
#define MAEA 17
#define MAEB 16

#endif

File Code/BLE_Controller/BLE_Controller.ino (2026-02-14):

/*
 * BLE HID Gamepad Example
 *
 * This example demonstrates how to create a BLE HID Gamepad device using ESP32.
 * The gamepad will appear as a standard HID game controller on Windows, macOS, Linux, Android, and iOS.
 *
 * Features:
 * - 8 buttons (mapped to buttons 1-8)
 * - 2 axes (X, Y for joystick movement)
 * - Secure pairing with bonding
 * - Battery level reporting
 * - Automatic reconnection after power cycle
 *
 * Usage:
 * 1. Upload this sketch to your ESP32
 * 2. Pair with your device (Windows: Settings > Bluetooth & devices)
 * 3. The gamepad will send test input (circular motion and button toggle)
 * 4. Test in any game or with gamepad testing tools like https://hardwaretester.com/gamepad
 *
 * Note: This example uses "Just Works" pairing for automatic connection without
 * PIN entry or confirmation, just like real gamepads. The bond is saved for future connections.
 *
 * Created by lucasssvaz
 */

#include <BLEDevice.h>
#include <BLEUtils.h>
#include <BLEServer.h>
#include <BLEHIDDevice.h>
#include <BLESecurity.h>

// GPIO defines
#define JOY_X 2
#define JOY_Y 3
#define BUT  4
#define SEL 15

// HID Report Descriptor for a gamepad with 8 buttons and 2 axes (X, Y)
// This descriptor defines the gamepad as having:
// - 8 buttons (usage buttons 1-8)
// - 2 8-bit axes (X, Y) with range -127 to 127
const uint8_t hidReportDescriptor[] = {
  0x05, 0x01,  // Usage Page (Generic Desktop)
  0x09, 0x05,  // Usage (Gamepad)
  0xA1, 0x01,  // Collection (Application)
  0x85, 0x01,  //   Report ID (1)
  0x09, 0x01,  //   Usage (Pointer)
  0xA1, 0x00,  //   Collection (Physical)
  0x09, 0x30,  //     Usage (X)
  0x09, 0x31,  //     Usage (Y)
  0x15, 0x81,  //     Logical Minimum (-127)
  0x25, 0x7F,  //     Logical Maximum (127)
  0x75, 0x08,  //     Report Size (8)
  0x95, 0x02,  //     Report Count (2)
  0x81, 0x02,  //     Input (Data, Variable, Absolute)
  0xC0,        //   End Collection
  0x05, 0x09,  //   Usage Page (Button)
  0x19, 0x01,  //   Usage Minimum (Button 1)
  0x29, 0x08,  //   Usage Maximum (Button 8)
  0x15, 0x00,  //   Logical Minimum (0)
  0x25, 0x01,  //   Logical Maximum (1)
  0x75, 0x01,  //   Report Size (1)
  0x95, 0x08,  //   Report Count (8)
  0x81, 0x02,  //   Input (Data, Variable, Absolute)
  0xC0         // End Collection
};

// Gamepad report structure (matches the HID descriptor)
struct GamepadReport {
  uint8_t reportId;  // Report ID (must be 1)
  int8_t x;          // X axis (-127 to 127)
  int8_t y;          // Y axis (-127 to 127)
  uint8_t buttons;   // 8 buttons (bit 0-7)
} __attribute__((packed));

BLEHIDDevice *hid;
BLECharacteristic *inputGamepad;
BLEServer *server;
bool deviceConnected = false;

// Server callbacks to track connection status
class ServerCallbacks : public BLEServerCallbacks {
  void onConnect(BLEServer *pServer) {
    deviceConnected = true;
    Serial.println("Client connected");
  }

  void onDisconnect(BLEServer *pServer) {
    deviceConnected = false;
    Serial.println("Client disconnected");
    // Restart advertising so we can reconnect
    BLEDevice::startAdvertising();
    Serial.println("Advertising restarted");
  }
};

// Security callbacks for "Just Works" pairing
class SecurityCallbacks : public BLESecurityCallbacks {
  bool onSecurityRequest() {
    return true;  // Accept all pairing requests
  }

#if defined(CONFIG_BLUEDROID_ENABLED)
  void onAuthenticationComplete(esp_ble_auth_cmpl_t auth_cmpl) {
    if (auth_cmpl.success) {
      Serial.println("Pairing successful!");
    } else {
      Serial.printf("Pairing failed, status: %d\n", auth_cmpl.fail_reason);
    }
  }
#elif defined(CONFIG_NIMBLE_ENABLED)
  void onAuthenticationComplete(ble_gap_conn_desc *desc) {
    if (desc->sec_state.encrypted) {
      Serial.println("Pairing successful!");
    } else {
      Serial.println("Pairing failed");
    }
  }
#endif

  // These are not used with "Just Works" pairing (ESP_IO_CAP_NONE)
  uint32_t onPassKeyRequest() {
    return 0;
  }
  void onPassKeyNotify(uint32_t pass_key) {}
  bool onConfirmPIN(uint32_t pass_key) {
    return true;
  }
};

void setup() {
  Serial.begin(115200);
  Serial.println("Starting BLE HID Gamepad");

  //PinModes
  pinMode(JOY_X, INPUT);
  pinMode(JOY_Y, INPUT);
  pinMode(BUT, INPUT);
  pinMode(SEL, INPUT);

  // Initialize BLE
  BLEDevice::init("ESP32-Gamepad");

  // Configure BLE Security for pairing and bonding
  // Use "Just Works" pairing - no user interaction required (like a real gamepad)
  BLESecurity *pSecurity = new BLESecurity();

  // Set IO capability to NONE (no display, no keyboard - like a real gamepad)
  pSecurity->setCapability(ESP_IO_CAP_NONE);

  // Set authentication mode: bonding=true, MITM=false, secure connection=true
  // This enables "Just Works" pairing with bonding
  pSecurity->setAuthenticationMode(true, false, true);

  // Set security callbacks
  BLEDevice::setSecurityCallbacks(new SecurityCallbacks());

  // Create BLE Server
  server = BLEDevice::createServer();
  server->setCallbacks(new ServerCallbacks());

  // Create HID Device
  hid = new BLEHIDDevice(server);

  // Set HID device information
  hid->manufacturer()->setValue("Espressif");
  hid->pnp(0x02, 0x05ac, 0x820a, 0x0110);  // Vendor ID, Product ID, Product Version
  hid->hidInfo(0x00, 0x01);                // HID version, country code

  // Set Report Map (HID descriptor)
  hid->reportMap((uint8_t *)hidReportDescriptor, sizeof(hidReportDescriptor));

  // Create input report characteristic for gamepad
  inputGamepad = hid->inputReport(1);  // Report ID 1

  // Set battery level to 100%
  hid->setBatteryLevel(100);

  // Start HID services
  hid->startServices();

  // Setup advertising
  BLEAdvertising *advertising = BLEDevice::getAdvertising();
  advertising->setAppearance(0x03C4);  // HID Gamepad appearance
  advertising->addServiceUUID(hid->hidService()->getUUID());
  advertising->setScanResponse(true);
  advertising->setMinPreferred(0x06);  // Help with connection issues
  advertising->setMaxPreferred(0x12);

  BLEDevice::startAdvertising();

  Serial.println("BLE HID Gamepad ready!");
  Serial.println("Waiting for connection...");
}
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

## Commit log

2026-01-28 Added PCB project files
    [Valdis.PrjPcb, Valdis.SchDoc]
2026-01-28 PCB 3D body exports and PDF export
    [Valdis.PrjPcb, Valdis.SchDoc]
2026-01-28 Added PCB pics
2026-01-30 Rev2 export
    [Valdis.xlsx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]
2026-01-30 Forgot to save
    [Valdis.PrjPcb]
2026-02-14 v0 done, competetion done, code uploaded, soon moving to RK github
    [Valdis.PcbDoc, Valdis.PrjPcb, Valdis.SchDoc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]
2026-02-17 rev1 pcb layout
    [Valdis.PcbDoc, Valdis.PrjPcb, Valdis.SchDoc]
2026-02-18 added v0.1 code
    [partitions.csv]
